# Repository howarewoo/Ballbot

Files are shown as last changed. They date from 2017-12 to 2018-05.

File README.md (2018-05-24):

 # Ballbot: a Dynamically Stable Omnidirectional Robot

A ballbot is a dynamically-stable mobile robot designed to balance on a single spherical wheel (i.e., a ball). Through its single contact point with the ground, a ballbot is omnidirectional and thus exceptionally agile, maneuverable and organic in motion compared to other ground vehicles. Its dynamic stability enables improved navigability in narrow, crowded and dynamic environments.

The ballbot works on the same principle as that of an inverted pendulum. As such, the ballbot can be broken down into three major components: The pendulum, the control system, and the drive unit. The pendulum component, and therefore the control system, can further be broken down from a single three dimensional coordinate system to pair of two dimensional coordinate systems.

Because the pendulum is broken down into two dimensional models, the control systems computes the required X and Y axis components to control the system. Using a linear quadratic regulator and discrete state space controller, the control system can use the angle from vertical to produce optimized control for the desired states. These states can be summed to represent a resultant vector in the XY plane.

This resultant vector can be converted to motor speeds though kinematic equations for the interaction between the motors, wheels, and ball.

CAPSTONE project by Adam Woo, Graham Goodwin, and Chloe Desjardins

## Mathematical Modeling

In essence, a ballbot is an omnidirectional inverted pendulum. This means that the ballbot can be broken down into two inverted pendulums that travel along the X and Y axis. The angle of the robot along these axis at any given time can be used to calculate the necessary velocity required to keep the pendulums upright.

The X and Y components can be summed to a desired resulting vector, which can be used to maintain the robots verticality in 3D space.

The state equations for an inverted pendulum can be represented as:

<p align="center">

</p>

<p align="center">

</p>

Where the variables are:

<p align="center">

</p>

These state space equations are used to produce a state space controller, where the output of the controller, , is the desired ball velocity along the X or Y axis.

These velocities can be plugged into a set of kinematic equations that calculate the required speed of each motor. The motor speeds much sum all torques around the Z axis to 0 for our system. These equations can be represented as such:

<p align="center">

</p>

<p align="center">

</p>

The scalar  accounts for the angle of the wheels relative the the center of the ball. This shifts the resultant velocity to the top surface of the ball.

To solve for the motor speeds, the inverse of the 3x3 matrix was found. When arranged to solve for the desired motor speeds, the equations look as follows:

<p align="center">

</p>

These equations can be used to calculate the desired speed of each motor in m/s, which can then be converted to steps/s based on the length of each step. The steps/s is the frequency at which pulses will be sent to the motor drivers.

Matlab was used for all of the control system modeling.

## Hardware

Here is a list of the selected hardware:

| Component | Part | Description |
| --- | --- | --- |
| Microcontroller | Teensy 3.6 | Faster processor speed, easy plug and play setup, and an extensive community make the Teensy 3.6 an ideal choice for the microcontroller over less powerful options like an Arduino Mega, or a less supported board. |
| IMU | MPU6050 | The 6 degrees of freedom supported by the MPU6050 allow for accurate angle measurements for a very cheap price. |
| Ball | 10" Stainless Steel Mirror Ball w/ Plastidip | A 10" steel ball provides a round ridged surface strong enough to support the robots chassis. The ball is coated in Plastidip, a rubberlike spray that will increase the friction on the ball. |
| Wheels | 3x 3.25" VexPro Omniwheel | Omniwheels allow for free movement perpendicular to the wheel. This allows for the development of holonomic movement systems. |
| Motors | 3x Nema 23 Stepper Motor | Stepper motors provide the high level of precision and torque at low speeds that the system will need to remain stable. |
| Motor Drivers | 3x TB6600 Stepper Motor Driver | These drivers allow the stepper motors to be controlled with only two data pins; one for direction and one for speed. |
| Battery | Gens ace 5000mAh 11.1V LiPo | The battery must be at least 9V. This battery was a highly rated battery with a large capacity, sufficient voltage, and relatively low weight. |
| Universal Battery Elimination Circuit | BW® RC Servo BEC UBEC 3A 5V | An UBEC is a voltage regulating circuit used to take power from the battery to the microprocessor. |

## Building Process

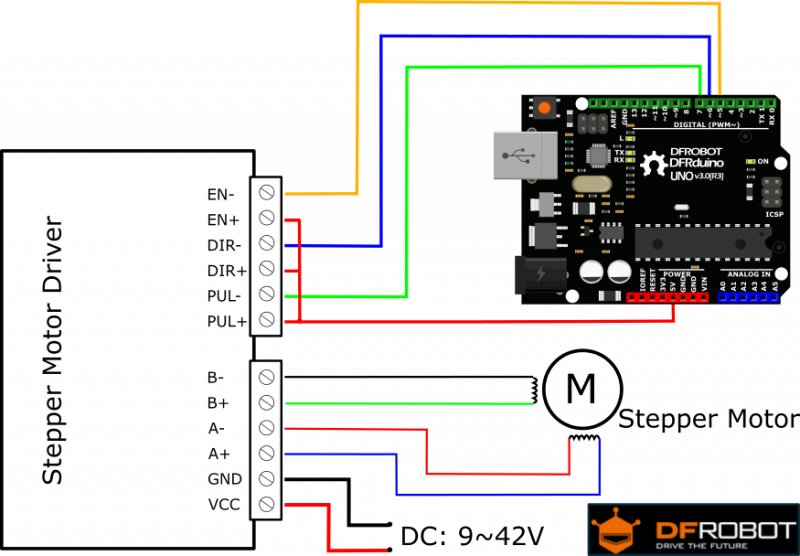
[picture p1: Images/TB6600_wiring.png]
TB6600 Wiring


The driver was manually set to the following:
- Microstepping: 1/8
- Current: 2.8A

The step pins output a square wave of varying frequencies. Pins 2, 3, and 5 where chosen because they all run on different timers. Therefore, the frequencies can be adjusted independently.

## Programming

All programming was done using the Atom text editor, Arduino IDE, and Teensyloader programs.

**Libraries**
- discreteSSC.h by Adam Woo
- quaternionFilter.h by Kris Winer
- Math.h
- Wire.h
- TimerOne.h
- FrequencyTimer2.h
- TimerThree.h

## Results

The ballbot provided limited stability for the 2D control systems. While this could be for several reasons, a likely reason for the instability is that there are forces not accounted for by a two dimensional model of the system.

The longest recorded stability of the robot was approximately 10 seconds.

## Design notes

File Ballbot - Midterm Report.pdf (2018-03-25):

### Ballbot Fall Semester Design Report:

### Design Process

Graham Goodwin, Adam Woo, Chloe Desjardins

Capstone I: ENGR 483
Professor Huang and Professor Mertens December 15th, 2017

Table of Contents

I. History of the Ballbot
In 2008, a team of graduate researchers at Carnegie Mellon University developed the first omnidirectional robot, capable of interacting in human environments. This design differed from other robotic designs in that for a robot to actively interact with human movement, an entirely different approach to locomotion must be implemented. The goal was to develop mobile robots that are safe, dynamically agile, and capable of graceful motion. The robot would be slender enough to easily maneuver in crowded, peopled environments, and readily yield when pushed around. In order to meet these design requirements, the team of researchers decided to create an intrinsically unstable robot which uses a ball for mobility. This new concept introduced the family of robotics to “ballbots.” Despite the capabilities of the omnidirectional machines known as ballbots, there has been little improvement made on the original designs.
In addition to the work done by the researchers at Carnegie Mellon University, some engineering students at ETH in Zurich have created a similar ballbot, using the concepts of stability and balance. This ballbot, named “Rezero,” has the ability to interact with humans, aims at high agility and fast movement, as well as create a hands-on experience with the Ballbot technology. Rezero’s dynamic hull allows the ballbot to display emotions such as breathing, being frightened, or waking up and going back to sleep.
As the ballbot technology continues to improve, there are a variety of ways that this type of robot can be advantageous in everyday life. For example, ball bots can serve as guides in museums or act as security monitors in public places. They can also be used as a daily aid, performing basic tasks such as transporting and delivering objects to humans. Ballbots can also be used as service robots assisting the disabled such as the blind. Due to the ballbot’s ability to navigate in cluttered environments and perform interference correction, the ballbot could potentially assist patients in hospitals.

II. Problem Definition
The primary objective of this project is to develop a single-contact, self balancing robot that is capable of omnidirectional movement.

III. Problem Evaluation
In order for this robot to perform in practical applications, several design criteria must be met. The ballbot must be slender enough to enable it to maneuver through crowded spaces. The body of the robot cannot be too wide, as the robot should take up as much walking space as a human at most. The ballbot must also be tall enough to interact with a standing human. Lastly, the ballbot needs to be capable of performing interference correction. This means that the ballbot can give in to small pushes, but then reset and continue on its trajectory. These three design goals correlate with the potential use cases for ballbots in that our ballbot will be capable of omnidirectional stabilization and agile movement in crowded environments.
We decided early on that humans should be able to easily interact with our system while standing, thus one of our primary design goals was to make the system at least three feet in height. Additionally, there would be little need for a single contact system unless it holds some advantages over multiple contact systems. A primary advantage of single contact systems is that the base can be quite narrow, even if the entire body is rather tall. This means that such systems can easily maneuver through crowded environments without sacrificing height. To play to this strength, we decided to aim for a system that would be slender, less than one foot wide.
Some goals were discussed but not established, such as speed, precision, carrying capacity, durability, interactability, and power consumption. However, we decided that these extra design goals were unnecessary or impractical for our purposes. These specifications were set as considerations, with the intention to optimize them as much as possible, but not to establish a specific requirement for project completion. With the design goals established, we moved on to address the design constraints of this project.
The first constraint established was time. The time limit for this was defined as slightly less than an academic year, accounting for presentations and analysis and the end of the year. Our group agreed that this was ample time for the projects main objective of designing a stationary balancing robot, with room to add movement or other aspects later down the line.
The second constraint addressed was cost. The Trinity College Engineering Department allocated $150 per student for their senior design projects. That means that our team of three was given a $450 budget. A quick look at the required equipment we might need to buy allowed us to estimate that we would have more than enough money to complete this project.

IV. Alternatives
Before weighing alternative parts for our system, we first had to decide on an overall design of the system. We looked at several examples of existing ballbots, some of which are displayed below:

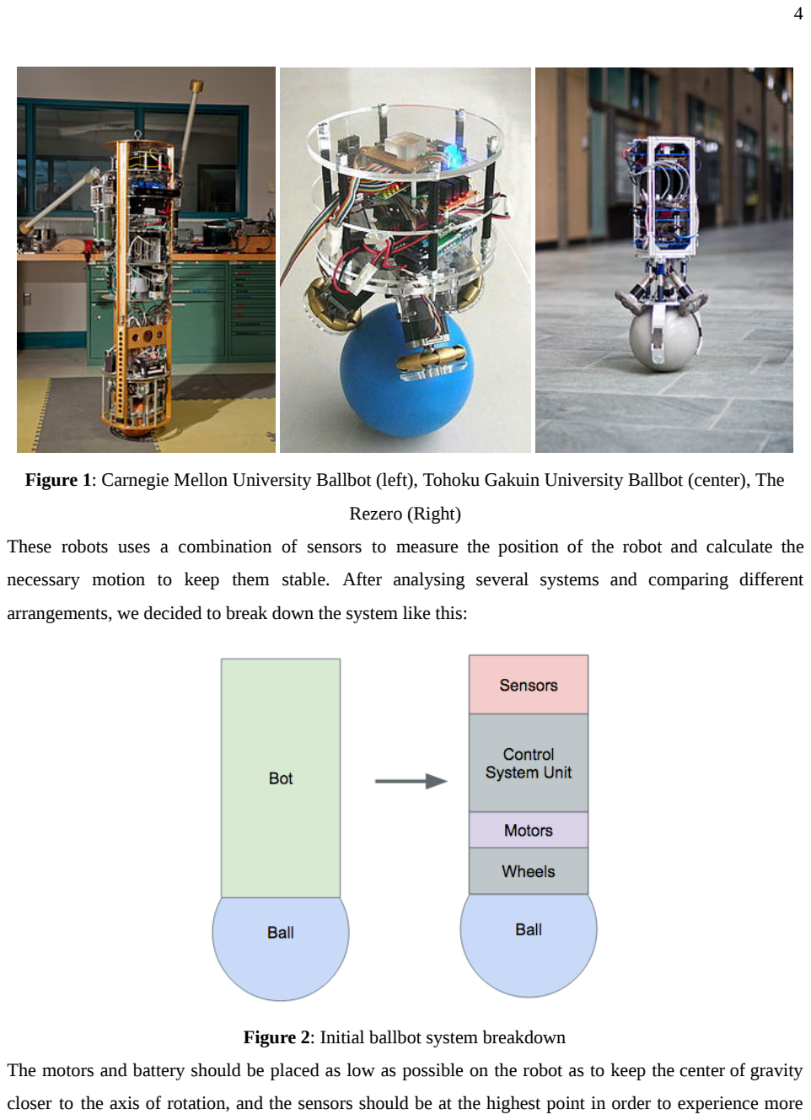
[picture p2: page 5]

Figure 1: Carnegie Mellon University Ballbot (left), Tohoku Gakuin University Ballbot (center), The Rezero (Right)
These robots uses a combination of sensors to measure the position of the robot and calculate the necessary motion to keep them stable. After analysing several systems and comparing different arrangements, we decided to break down the system like this:

Figure 2: Initial ballbot system breakdown The motors and battery should be placed as low as possible on the robot as to keep the center of gravity closer to the axis of rotation, and the sensors should be at the highest point in order to experience more exaggerated movement for measurement. The components of the control system should weigh little enough that their placement should have a negligible impact on the system’s stability.
With a tentative structure of the robot designed, we began analysing alternatives for each component.

The Ball
From our design goals, we knew we wanted the base of the system to be less than one food wide, and thus we only considered types of balls whose diameters were about that wide.
From our problem evaluation, we knew that a lightweight ball would require less torque from the motors to move. Thus, we tried to strike a balance between weight and functionality when choosing the ball. We researched the following alternatives, and listed the pros and cons of each:
Table 1: Ball Alternatives with Pros and Cons
Name | Pros | Cons
Bowling Ball | -rigid surface -good quality control (close to perfectly spherical) | -slippery surface -requires excessive torque from motors -expensive (~$40)
Steel “Mirror Ball” Lawn Ornament | -hollow (less torque required) -rigid surface | -slippery surface -expensive (~$30)
Hollow Plastic Ball | -low mass (little torque required for motion) -Inexpensive (<$10) | -flexible surface -slippery surface
Basketball | Inexpensive (~$10) -low mass -surface has high coefficient of friction | -ridges on surface introduce error/potential failure of system -not entirely spherical

While each of the alternatives above have their own merits, we decided that we could best work around the shortcomings of the steel mirror ball. The bowling ball had all of the shortcomings of the mirror ball in addition to the excessive torque requirements it would place on the motors. The benefits did not seem to outweigh this issue, so we eliminated the bowling ball alternative. A bowling ball is also relatively expensive ($40), thus we decided that this was not the best fit for our system.
The only real benefit of the hollow plastic ball was that it was extremely cheap, however, since the other alternatives were well within our budget, price was not a major concern. So we quickly eliminated the plastic ball alternative as well.
The basketball was a close contender with the mirror ball. It would provide good grip for the wheels on the surface of the ball, and was lighter than the mirror ball by about 0.3 kg. However, the ridges on the basketball would introduce error into our system. It would be near impossible to predict when the wheels would be rolling over one of the basketball ridges, and thus some varying degree of unknown error would be introduced. We were already getting a sense of the complexity of the mathematical system behind the ballbot, so we decided to pursue the mirror ball alternative. To counteract the slippery surface of the mirror ball, we came up with the idea of coating it in plastic spray. This would eliminate the surface grip problem, and since the price was within our original cost estimate, we were satisfied with this alternative.
Chosen Alternative: Steel mirror ball with plasti-dip coated surface
- Size: 10” diameter (near perfect sphere)
- Weight: 0.91 kg
- Total Cost: $45 ($35 + $10 for plasti-dip)

The Microcontroller
In order to control a dynamically stable system, the microprocessor needs to be able to communicate with sensors, calculate the raw data through a control system, and send the control signals to the motors extremely quickly. The main issue with this design is that the control system is complex, involving several trigonometric calculations and filters which are very processor intensive. The microcontroller needs to have a processor capable of computing these calculations quickly.
Additionally, we wanted to program the controller using our language of choice, C++. We use the Atom text editor plugin PlatformIO to write, build, and upload our programs to various microcontrollers. While this is not a restriction for our system, it was an ease of use factor which influenced our decision. To decide on a microcontroller, we researched what had been used for several other ballbots. The main alternatives to decide between were as follows:

Table 2: Microcontroller Alternatives with Pros and Cons

Name | Pros | Cons
Arduino Mega | ● already owned (~$10 otherwise) ● PlatformIO bootloader compatible ● 54 programmable pins | ● 8 Mhz clock speed
Raspberry Pi 3 Model B | ● 1.2 GHz clock speed ● 26 programmable pins ● Large community ● USB power ● Expandable | ● expensive (~$35) ● Complex library setup ● Not PlatformIO compatible
Teensy 3.6 | ● 180 MHz clock speed ● PlatformIO bootloader compatible ● 32 programmable pins ● Arduino library compatible ● Micro USB power port | ● expensive (~$40)

After extensive research on what microcontroller would be the most efficient to use, we decided to choose the Teensy 3.6. Initially, we were going to use a Raspberry Pi because of its familiarity and its extensive community support. However, after performing further problem evaluation, we decided to go with the Teensy 3.6 due to its larger number of programmable pins (32), high processing speed (180 MHz), and good compatibility with our IMU and it’s fusion libraries (more on this later).
Chosen Alternative: Teensy 3.6
- Processor Speed: 180 MHz
- Cost: $40

The Ball Drive System
The parts in contact with the ball needs to allow movement in all directions. The parts cannot restrict range of motion in any why. The type of ball drive system was relatively easy to chose, as majority of the alternatives were either too difficult to build, or would not work all together.
Table 3: Wheel Alternatives with Pros and Cons
Name | Pros | Cons
Partially Sliding Rollers | ● Inexpensive | ● Cannot be purchased ● Difficult to build
Omni-wheels | ● Easily purchased ● Passive lateral movement | ● Low strength ratings for cheaper models ● Non standard mounting options
Mecanum wheels | ● Easily purchased ● Inexpensive ● Higher strength ratings | ● No passive lateral movement (active movement only)
Spherical Induction Motor | ● Single moving part ● Highly accurate motion | ● Cannot be bought ● Very complex to build

Omni wheels were the only movement system that was feasible for this project. The mecanum wheels restricted movement laterally, and the other two systems were two difficult to design in the given time period. While the type of ball drive system itself was easy to chose, the design of this system was more difficult to agree upon. We looked at several different orientations for the wheels:

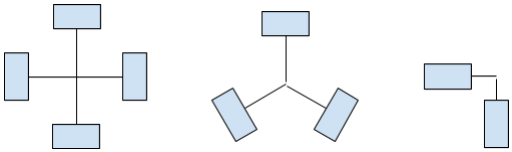
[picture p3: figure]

Figure 3:Various wheel arrangements

The first orientation we looked at was the four wheeled design which maps two wheels to each axis. This was a good design and easy to control. However, omni wheels and the motors required to drive them are expensive, as well as heavy. To cut down on these costs, we looked at a two wheeled model which used point the wheels towards the center of the robot. This gave us control over the x and y axis, but removed the possibility of rotation. The compromise was a three wheeled design spaced evenly apart, which the wheels placed perpendicularly to the robot’s center. The wheels would be angled at 45 degrees and placed 45 degrees from the ball’s center to maximize control over all axis of rotation.

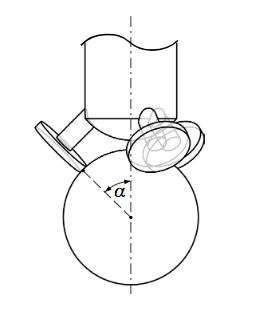
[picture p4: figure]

Figure 4: The three wheeled design of the ball drive system, where α=45° This design maximizes control over the ball, while minimizing the weight and cost of the system. Chosen Alternative: Three omni wheels
- Manufacturer: Vex Pro
- Size: 3.25” diameter
- Total Weight: 0.54 kg (3 wheels, 0.18 kg each)
- Total Cost: $54 (3 wheels @ $18 each)

The Angle Measurements Devices
For these type of projects, inertial measurement units (IMUs) are the most widely used by far. There really were no other alternatives to decide between for measuring the robot angle from vertical. Among IMUs, the MPU6050 and MPU9250 were the two alternatives we considered.

Table 4: IMU Alternatives with Pros and Cons

Name | Pros | Cons
MPU6050 | ● 6 axis (accelerometer, gyroscope) ● Inexpensive ($7) | ● -no magnetometer (cannot measure compass direction)
MPU9250 | ● 9 axis (accelerometer, gyroscope, magnetometer) ● More precise measurement after filter | ● More complex filters ● Less community support ● Less board compatibility ● Slightly more expensive ($10)

The MPU9250 was the most suitable option compared to the MPU6050. Although the MPU6050 is three dollars cheaper than the MPU9250, the MPU9520 has 9 axes with an accelerometer, gyroscope and magnetometer. The MPU9520 is also capable of measuring compass direction. When considering our future goals for the movement of our ballbot, these additional capabilities of the MPU9520 were enticing and seemed more practical for our ballbot design. The price of the MPU9520 was also still within our economic means.
Chosen Alternative: MPU9250
- Functionality: 3-axis accelerometer (angular acceleration), 3-axis gyroscope (angular velocity), 3-axis magnetometer (compass direction)
- Cost: $10

The Motors
To drive the wheels, we required motors with relatively high torque at low speeds that could handle precise movement and change direction quickly. This indicated to us that stepper motors would likely be the best choice, though we did consider brushless DC motors as well.

Table 5: Motor Alternatives with Pros and Cons

Name | Pros | Cons
DC Brushless Motors | ● Inexpensive ● High RPM ● PWM | ● Lower torque ● Ramping acceleration
Stepper Motors | ● High torque at low speeds ● Precision movements | ● More expensive ● No PWM

We decided to use stepper motors for our system, because of their high torque at low speeds and precise movement options. We decided to use an a4988 stepper motor driver to control and power them. We also decided to use a motor that fits the NEMA 23 standard. This allows us to start designing the mounting hardware, even though we do not know the exact model we will be using.
We have not yet decided on a model because we want to make sure the rated torque is high enough for our system, which requires the math modeling to be completed first. The NEMA 23 comes in a variety of lengths, the longer the motor the higher the torque. We will purchase the motors early next semester.

### Ballbot Fall Semester Design Report:

### Full System Design Description

Graham Goodwin, Adam Woo, Chloe Desjardins

ENGR 483: Engineering Capstone I

December 15, 2017

Introduction
The following document details our current full-system design. It serves as an overview of the subsystems we have identified, as well as the completion levels of those systems.

Current System Design
We identified the following subsystems of the ballbot:
1. Chassis
2. Inertial Measurement Unit System (9-axis IMU)
3. State observer system (microprocessor)
4. Controller system (microprocessor)
5. Ball drive system
6. Power system
After going through the problem evaluation process and weighing alternatives, we arrived at our current full-system design. A physical layout of the system can be seen below.

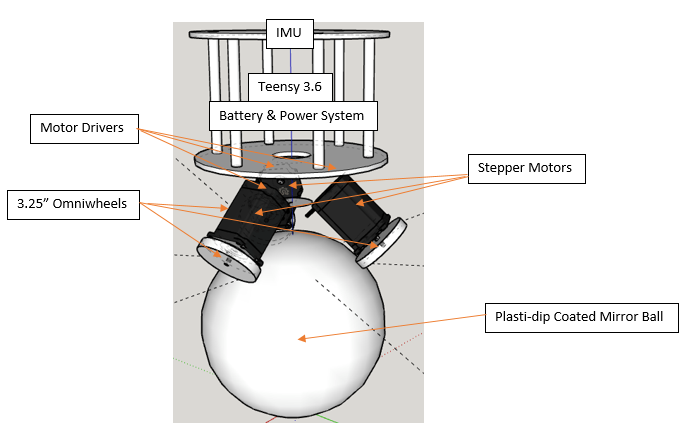
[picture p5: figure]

Figure 5: Full-system Physical Layout

We also constructed a block diagram depicting how the system components will interact (seen below).

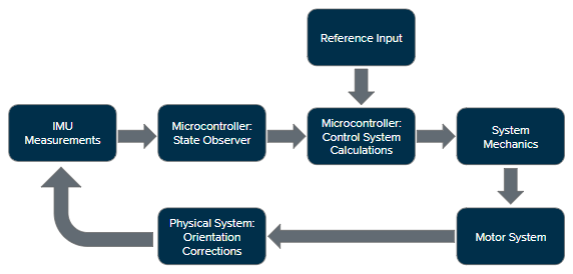
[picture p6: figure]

Figure 6: Full system block diagram

Chassis
The chassis design for the system was kept very simple with only the purpose of housing the other components. We chose a 10” diameter circular platform design that can be easily raised and lowered depending on the size of the parts. One platform will attach to the motor mounts, and hold the battery and motor drivers on it. The middle platform will hold the microprocessor, and the top platform will have the IMU mounted to the bottom of it. The platforms will be held together using six ¼” threaded rod and held in place with twelve ¼” nuts and washers for each platform. This allows the platforms to be moved according to the needs of the system, but still remain secure when desired.

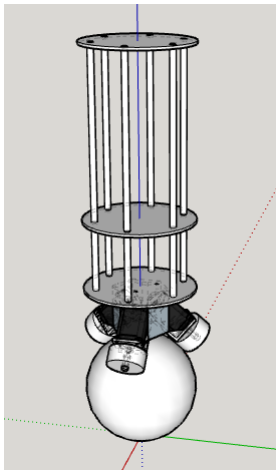
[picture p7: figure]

Figure 7: Full size CAD model of the ballbot

IMU System
The MPU9250 consists of an accelerometer, gyroscope, and magnetometer, which read angular acceleration, velocity, and compass readings respectively and communicates them to the microcontroller using I2C. These sensors supply three raw data points each, one for each axis, for a total of nine data points. In order to convert these data points into understandable Euler angles (pitch, roll, and yaw), we need to first put these points through sensor fusion, a method of combining the readings to reduce noise and minimize calculation error. Our chosen method of sensor fusion was Sebastian Madgwick’s Orientation Filter, seen below:

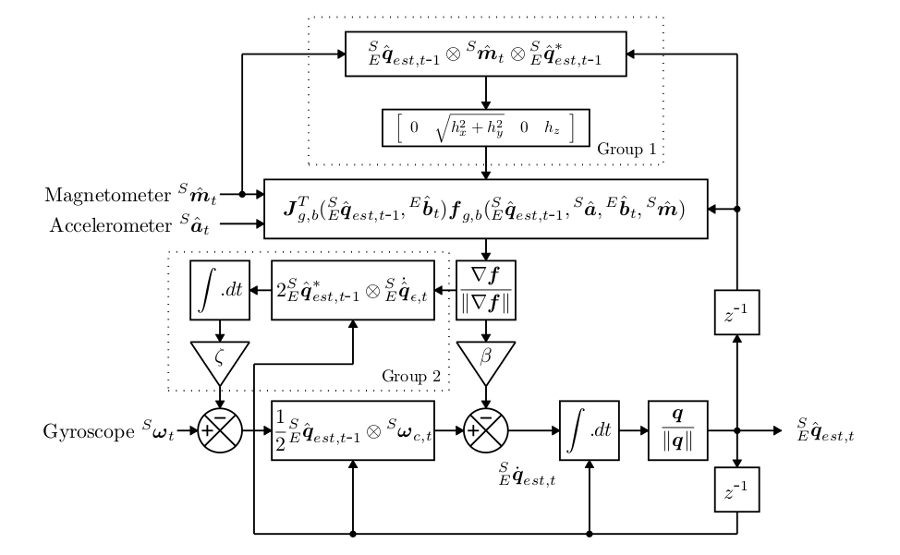
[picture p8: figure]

Figure 8: Sebastian Madgwick’s Orientation Filter This sensor fusion algorithm inputs the data from the three measurement tools and outputs a quaternion, which is essentially a four dimensional unit vector. This quaternion can be used to find Pitch, Roll, and Yaw using the following equations:

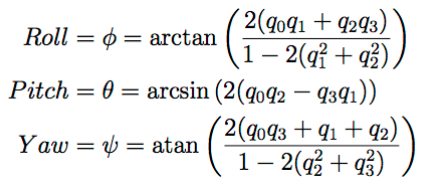
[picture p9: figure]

This method was chosen because it is one of the most accurate methods for calculating the angular position. It is also open source which allowed us to use pre existing C++ libraries and modify them for our specific IMU. We have already implemented this our our microprocessor and tested the accuracy of our readings. Sebastian Madgwick claims that this algorithm is precise to less than a degree of error.

State Observer
The state observer system is a project for next semester, but we know that it will take in the Euler angles generated by the IMU calculations and output the system states, i.e. the angle from vertical and its velocity, and the angular position of the ball and it’s velocity.

Control System
We have explored several options for controlling our system, but have yet to decide on a final method. The first method would be to use a proportional integral derivative control (PID) to control by calculating the required gains for our unique transfer function, and then refining the controls empirically. We also explored linear quadratic regulator (LQR) controls, which is an optimizing form of control that aims to minimize some user-defined cost function. In our case, that cost function would be the systems angle from vertical.
Regardless of the control method, the inputs would be the desired angles from vertical in the z-x and z-y planes. The feedback would come from the IMU which depending on the difference between the desired angle and the actual angles, return the required x and y velocities for the ball to stabilize the system. The ball drive system will take the desired x and y velocities and convert them to the appropriate motor speeds to move the ball the desired resultant vector.

Ball Drive System
The ball drive system is made up of the motor drivers, the motors, and the wheels. The a4988 stepper motor drivers power the motors and control their speed via their connection to the microprocessor. Stepper motors have a high torque at low speeds which will allow for quick changes of direction. The wheels are connected the motors by a custom designed 3d printed wheel hub.
We opted for a three wheeled design to cut down on weight and cost, as opposed to a four wheeled design. Despite the mechanical advantages of this orientation this design does presents a difficulty in controlling the motors there are no two wheels mapped to each axis. This means that a series of motor speed equations will need to be developed to move the ball correctly. By drawing out the wheel orientations as such:

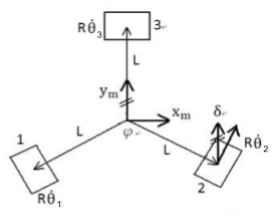
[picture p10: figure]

Figure 9. Kinematics of robot movement in the x-y plane

Here, δ is the angle between the wheel and the axle (90°), and φ is the angle between the center of each wheel (120°). This leaves us with these equations:
θ̇1 = R

ẋ− ẏ+Lϕ̇ 2

1
| 2

√3

θ̇2 = R

ẋ+ ẏ+Lϕ̇ 2

1
| 2

√3

θ̇3 = R

ẋ+Lϕ̇

Where θ̇ is the angular velocity of the motor, L is the distance from the center of the robot, and R is the

wheel radius. We can find trigonometric equations that sum the velocity vectors of the motors to give a single velocity vector in a desired direction from the robot’s center:

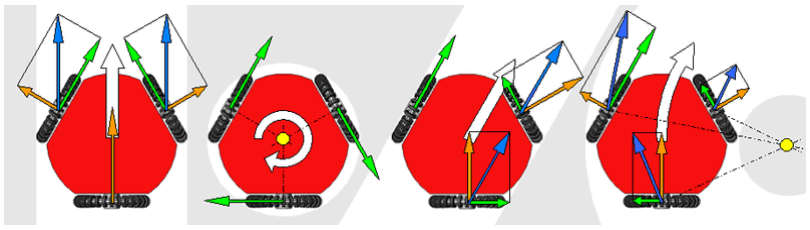
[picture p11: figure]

http://3.bp.blogspot.com/_a_6DwTj3ij0/TRxY3TovHHI/AAAAAAAAAGc/OVVlBWgrc5g/s1600/800px-robot_omnidirectional_movement_spe edvectors.gif
Figure 10: Examples of potential movement patterns for the ball bot as a sum of the wheel velocities (green arrows)

Because we know the size of our wheels and our ball, we can find the values of L and R to plug into these equations:
L = √ | .755in

π

√10in −(5in(sin(45)))
2 | 2 ≈ 1
R = | .625in
2

3.25in = 1

Which leaves us with:
θ̇1 = | .308ẋ | .533ẏ | .08ϕ 1.625

ẋ− ẏ+1.755ϕ̇ 2

1
2

√3
≈ 0 | − 0 | + 1
θ̇2 = | 1.625

ẋ+ ẏ+1.755ϕ̇ 2

1
2

√3

## ≈ 0.308ẋ+ 0.533ẏ+ 1.08ϕ

θ̇3 = 1.625

.08ϕ

ẋ+1.755ϕ̇
≈

ẋ
1.625 + 1

These equations can be used to take the desired system velocities given by the controller, and convert them into equivalent motor speeds.
The omni wheels have a rubber texture on the rollers, and the ball is coated in plastidip to increase its traction.

Power System
The power system, so far has been an afterthought. We know that the motors operate on 5.4V at 1.5A, while the Teensy 3.6 runs on a 5V input. We need to do more research on the battery and power supply system, but the basic wiring for the motors and drivers will look like this:

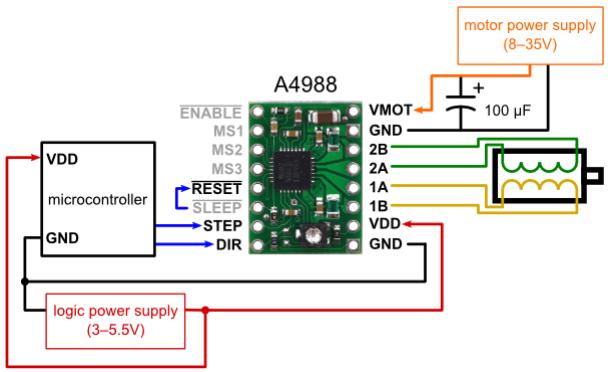
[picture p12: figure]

Figure 11: Circuit diagram for the a4988 motor drivers

Math Modeling
We started with a 2D planar model of the system. We start with a 2D model because the xz and yz planes of the robot are identical. The full system is then controlled by breaking each motor force into components in the xz and yz planes.

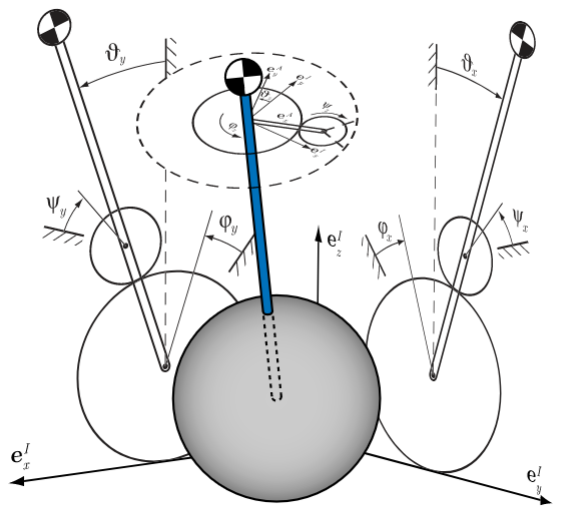
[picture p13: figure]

Figure 12: The 2D breakdown of the 3D system Analyzing the system in this manner will give us a desired velocity for the x and y components and sent direction to the motor equations. The predicted result will be 3D stabilization as the combination its components.
We have not yet explored the intricacies of coupling these planar models, but the hope is that this method will give a close enough estimation of the system controls to be modified empirically.

System Completion Percents
To assess our work over the past semester, as well as clarify what needs to be done going forward, we assigned completion levels to each of the subsystems we identified. For each subsystem, a percentage has been assigned to signify how complete it is, and a second percentage has been assigned to show if the physical components have been acquired yet. These can be seen below in Table 1, along with some details on what is complete, and what is left to do.

Table 6: Subsystem Physical and Design Completion Levels

Name of System | Level of Completion | Parts Acquired | Details
Chassis | 80% | 0% | CAD model finished, parts are not 3D printed
IMU System | 100% | 100% | IMU purchased, code implemented to output pitch, roll, yaw
State Observer | 10% | N/A (microprocessor) | States decided upon, need to research how to build state observer
Controller System | 50% | N/A (microprocessor) | PID and LQR researched, need to incorporate it into our model
Ball Drive System | 80% | 60% | Ball, plasti-dip, omniwheels and motor drivers purchased, need to purchase motors
Power System | 10% | 0% | Need to decide on and purchase battery
Math Modeling | 60% | N/A | 2D model completed, need to research coupling between 2D planar models

Spring Semester Goals
After assessing our progress thus far, we have a variety of goals that must be considered and achieved for the spring semester. Firstly, we need to complete the modeling of the system such as the Computer Assisted Design (CAD) modeling and the design of the chassis. After performing various calculations on the motors this semester, we have three separate motor equations, one for each motor. These motors that will be used to move the omni-wheels must still be purchased. Although we have already acquired majority of the hardware for our system, we still need to obtain several components such as the battery. Once all necessary parts are secured, we can then assemble the physical system. We will also complete the controller design and implement the control in code using C/C++. Once all of these goals are achieved, we will then proceed to test the system and tune the controller in order to achieve stability. Lastly, if time permits, we will ultimately implement remote controls or tracking for our ballbot.

Appendix
Meeting Minutes
Below is a summary of our meeting minutes with Professor Huang. We met (officially) every Friday at 10 am in order to discuss our progress and set our goals for the following week.

Capstone Meeting: Friday 11/03/17 - all members present
Plaster dip or rubber spray for the ball - cheapest
Stepper motors - need enough torque to get ball moving
Need stepper motor controllers
Need inputs
Stepper motor driver - power driver individually, need 4 pins, can do it directly from power source Need some sort of wedge to provide for angles, mount it to bottom of platform - use aluminum

Ball - $35
-10 in diameter

Omni-wheels -
-2-4 in in diameter?

How are we going to mount omni-wheels to the motors?
-Axle mount?

Arduino coded in C++ so we can convert to Raspberry Pi if needed -Arduino is cheaper than Raspberry Pi
-Make sure it works with Arduino first because we are all familiar with it

Want a prototype by the end of the semester!!!

Batteries
RC batteries

Acrylic components, 3D printing a prototype test base

Equations
Kinematic equations for motors, not sure if we need them to actually make the robot work, throw PID onto board and it will compensate
-Need to model how our control inputs are going to affect our states
Model using physical equations- how the motors will affect the ball moving around, torques and pendulums
Control theory- look into building an observer, get into algebra and talk about observability and controllability space

Look over theses for designing a ball bot to get an idea of what equations of motions will look like

Things we need to accomplish for next week:
-Look into ACS stuff
-Modeling/Kinematic Equations
-Design chassis (base)
-Axle mounts
-Ordering parts: ball, new IMUs, motors, driver chip A4888 -Find suitable batteries

Assignments:
Graham
-Modeling/Kinematic Equations

Adam
-Design chassis (axle mount)
-Begin coding
-Kinematics Equations for motor speed

Chloe
-Look into ACS stuff
-Find suitable batteries

Mutual:
Ordering ball, IMUs, motors, driver A4888, rubber coat
-Order ball, IMUs, driver A4888, rubber coat ($5) hold off on omni-wheels

Meeting minutes Friday 11/10/17 - all members present

- Model 3 motors on the ball separately using trigonometry in 3D then sum them together -Forces from the wheels
-Pendulum falling in the plane
-Then put these equations in block diagram as parameters
-3 planar model method
- Write state space equations, block diagram, feedback of 1 -Design for particular step response
-8 states total
- Response time - assume instantaneous
- Estimator? LQR/LQG?
- PID Controller

For the next 2 weeks:
-Motors
-Wheels
-Consider use cases
-Continue math modeling, research coding techniques

Graham:
-Continue math modeling

Adam:
-Researching coding techniques
-CAD model chassis
-CAD model and print custom mounting hardware

Chloe:
-Look into use cases
-Batteries

Mutual:
Purchase motors and omni-wheels

Meeting Minutes Friday November 17 - all members present
- Raspberry pi came, MPU
- More math modeling - turn into 3D
- Inverted pendulum project?
- NiMH 3-5 Ah - look up what hobbyists have used
- Lithium iron phosphate - any 5 Ah
- Buy batteries cheap to buy a few and keep cycling them
- Mechanical model by the end of the semester in google sketch-up
- Bought: raspberry pi, plasti-dip, ball, smaller electronics
- Stepper motors, have drivers
- Omni-wheels and motors are most important
- Heavier or lighter wheel based on inertia?
- Omni-wheels on the smaller side to get a faster response, need faster RPM : 2-4 in in diameter

Progress presentation for next Tuesday (post Thanksgiving) - start working on this
Continue with what we are doing….

Things we need to do:
-Buy omni-wheels, motors, batteries
-hobbyking.com, look at best selling battery and buy it -CAD modeling, MPU testing
-Start using Raspberry pi

Meeting Minutes 12/4/17 - Professor Mertens, all members present
- Need to calculate max angular acceleration that we want to impart on the ball
- Find torque in relation to axis of the ball
- The torque that the motor needs depends on the motor arm
- Ball moves by applying a tangential force
- Ɑ = ??, how quickly must we accelerate the ball?
- **Need to account for slippage**
- Quantify our design criteria - create a robust theoretical model
- “Subprojects” - a) dynamic analysis of the moving ball, b) microprocessor, c) motors, d) feedback loop
- For Traveler’s Presentation on 12/12/17: Show current design, components, here is what we have completed…
- Make sure to highlight which topic from the outline we are discussing during the presentation...Makes it easier for the listener to follow along and makes things less complicated

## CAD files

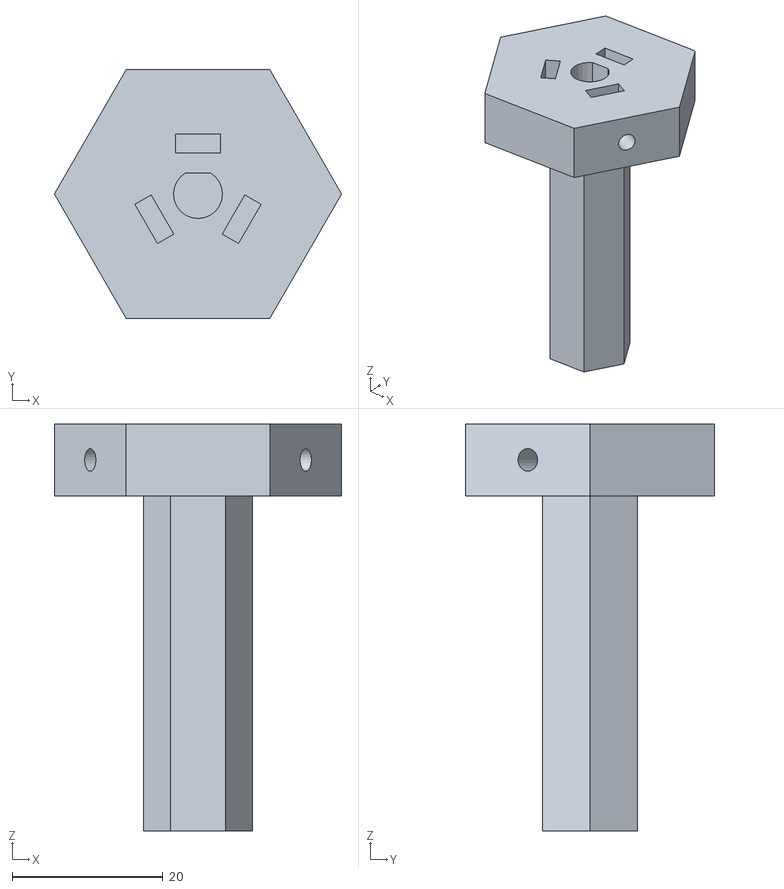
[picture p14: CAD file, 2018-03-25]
CAD/Wheel Mount.stl
38.1 x 33.0 x 54.0

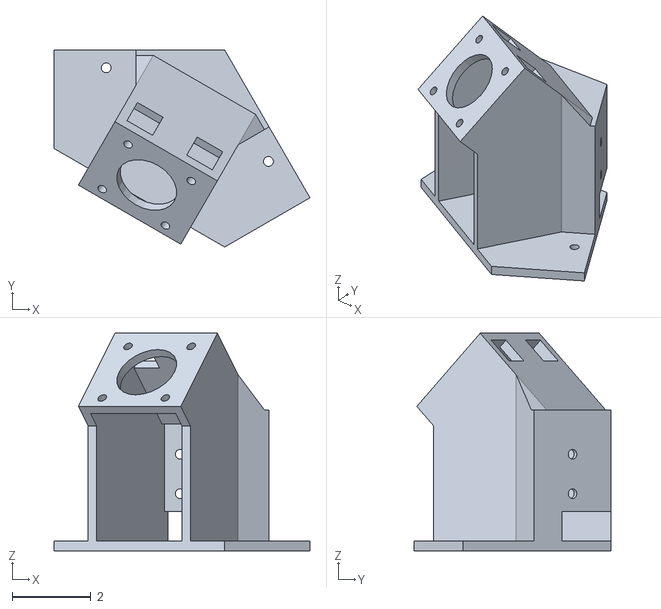
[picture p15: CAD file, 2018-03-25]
CAD/Ballbot Motor Mount v.3.stl
6.50 x 5.00 x 5.52

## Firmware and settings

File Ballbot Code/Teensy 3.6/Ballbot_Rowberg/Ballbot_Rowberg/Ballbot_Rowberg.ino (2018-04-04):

/* Ballbot_MPU6050.ino
*
* Omnidirectional Ballbot control system with 3-axis PID controls using the
* MPU6050 IMU
*
* Written by Adam Woo
*
* MIT License
*/

#include "math.h"
#include "PID_v1.h"
#include "FrequencyTimer2.h"
#include "TimerOne.h"
#include "TimerThree.h"

#define ROBOT_HEIGHT 31 //inches
#define WHEEL_RADIUS 1.625
#define STEPS_PER_ROTATION 6400 //steps
#define MAX_SPEED 120 //inches per second
#define MAX_FREQ 2000 //component steps per second
#define ACCEL 2000 //steps per second


int sampleRate =  10000; //microseconds
bool printFlag = false;

#define DIR1 12
#define STEP1 2
#define DIR2 24
#define STEP2 3
#define DIR3 26
#define STEP3 5

//Three PID controllers; one for each axis of rotation
//Define Variables we'll be connecting to
double CurrentAngleX, OutputSpeedX, DesiredAngleX = 0;
double CurrentAngleY, OutputSpeedY, DesiredAngleY = 0;
double CurrentAngleZ, OutputSpeedZ, DesiredAngleZ = 0;
double Kp_x=10, Kp_y=10, Kp_z=10;
double Ki_x=1, Ki_y=1, Ki_z=1;
double Kd_x=2, Kd_y=2, Kd_z=2;

//Specify the links and initial tuning parameters
PID xPID(&CurrentAngleX, &OutputSpeedX, &DesiredAngleX, Kp_x, Ki_x, Kd_x, DIRECT);
PID yPID(&CurrentAngleY, &OutputSpeedY, &DesiredAngleY, Kp_y, Ki_y, Kd_y, DIRECT);
PID zPID(&CurrentAngleZ, &OutputSpeedZ, &DesiredAngleZ, Kp_z, Ki_z, Kd_z, DIRECT);

#define AHRS true         // Set to false for basic data read
#define SerialDebug true  // Set to true to get Serial output for debugging

// -----------------------------------------------------------------------------
// Need this to compile for some reason... No idea why. Think it has something
// to do with the way the Teensy loader works
extern "C"{
  int _getpid(){ return -1;}
  int _kill(int pid, int sig){ return -1; }
  int _write(){return -1;}
}
// -----------------------------------------------------------------------------

// Pin definitions
int Pin = 12;  // These can be changed, 2 and 3 are the Arduinos ext int pins
int RPM = 0;

double speed1, speed2, speed3;
double timer = 0, timerstart, timerend;
double yaw, pitch, roll;
int currentSpeed1, currentSpeed2, currentSpeed3;

// I2C device class (I2Cdev) demonstration Arduino sketch for MPU6050 class using DMP (MotionApps v2.0)
// 6/21/2012 by Jeff Rowberg <jeff@rowberg.net>
// Updates should (hopefully) always be available at https://github.com/jrowberg/i2cdevlib
//
// Changelog:
//      2013-05-08 - added seamless Fastwire support
//                 - added note about gyro calibration
//      2012-06-21 - added note about Arduino 1.0.1 + Leonardo compatibility error
//      2012-06-20 - improved FIFO overflow handling and simplified read process
//      2012-06-19 - completely rearranged DMP initialization code and simplification
//      2012-06-13 - pull gyro and accel data from FIFO packet instead of reading directly
//      2012-06-09 - fix broken FIFO read sequence and change interrupt detection to RISING
//      2012-06-05 - add gravity-compensated initial reference frame acceleration output
//                 - add 3D math helper file to DMP6 example sketch
//                 - add Euler output and Yaw/Pitch/Roll output formats
//      2012-06-04 - remove accel offset clearing for better results (thanks Sungon Lee)
//      2012-06-01 - fixed gyro sensitivity to be 2000 deg/sec instead of 250
//      2012-05-30 - basic DMP initialization working

/* ============================================
I2Cdev device library code is placed under the MIT license
Copyright (c) 2012 Jeff Rowberg

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
THE SOFTWARE IS PROVIDED "AS IS", WITHOUT WARRANTY OF ANY KIND, EXPRESS OR
IMPLIED, INCLUDING BUT NOT LIMITED TO THE WARRANTIES OF MERCHANTABILITY,
FITNESS FOR A PARTICULAR PURPOSE AND NONINFRINGEMENT. IN NO EVENT SHALL THE
AUTHORS OR COPYRIGHT HOLDERS BE LIABLE FOR ANY CLAIM, DAMAGES OR OTHER
LIABILITY, WHETHER IN AN ACTION OF CONTRACT, TORT OR OTHERWISE, ARISING FROM,
OUT OF OR IN CONNECTION WITH THE SOFTWARE OR THE USE OR OTHER DEALINGS IN
THE SOFTWARE.
===============================================
*/

// I2Cdev and MPU6050 must be installed as libraries, or else the .cpp/.h files
// for both classes must be in the include path of your project
#include "I2Cdev.h"

#include "MPU6050_6Axis_MotionApps20.h"
//#include "MPU6050.h" // not necessary if using MotionApps include file

// Arduino Wire library is required if I2Cdev I2CDEV_ARDUINO_WIRE implementation
// is used in I2Cdev.h
#if I2CDEV_IMPLEMENTATION == I2CDEV_ARDUINO_WIRE
    #include "Wire.h"
#endif

// class default I2C address is 0x68
// specific I2C addresses may be passed as a parameter here
// AD0 low = 0x68 (default for SparkFun breakout and InvenSense evaluation board)
// AD0 high = 0x69
MPU6050 mpu;
//MPU6050 mpu(0x69); // <-- use for AD0 high

/* =========================================================================
   NOTE: In addition to connection 3.3v, GND, SDA, and SCL, this sketch
   depends on the MPU-6050's INT pin being connected to the Arduino's
   external interrupt #0 pin. On the Arduino Uno and Mega 2560, this is
   digital I/O pin 2.
 * ========================================================================= */

/* =========================================================================
   NOTE: Arduino v1.0.1 with the Leonardo board generates a compile error
   when using Serial.write(buf, len). The Teapot output uses this method.
   The solution requires a modification to the Arduino USBAPI.h file, which
   is fortunately simple, but annoying. This will be fixed in the next IDE
   release. For more info, see these links:

   http://arduino.cc/forum/index.php/topic,109987.0.html
   http://code.google.com/p/arduino/issues/detail?id=958
 * ========================================================================= */



// uncomment "OUTPUT_READABLE_QUATERNION" if you want to see the actual
// quaternion components in a [w, x, y, z] format (not best for parsing
// on a remote host such as Processing or something though)
//#define OUTPUT_READABLE_QUATERNION

// uncomment "OUTPUT_READABLE_EULER" if you want to see Euler angles
// (in degrees) calculated from the quaternions coming from the FIFO.
// Note that Euler angles suffer from gimbal lock (for more info, see
// http://en.wikipedia.org/wiki/Gimbal_lock)
//#define OUTPUT_READABLE_EULER

// uncomment "OUTPUT_READABLE_YAWPITCHROLL" if you want to see the yaw/
// pitch/roll angles (in degrees) calculated from the quaternions coming
// from the FIFO. Note this also requires gravity vector calculations.
// Also note that yaw/pitch/roll angles suffer from gimbal lock (for
// more info, see: http://en.wikipedia.org/wiki/Gimbal_lock)
#define OUTPUT_READABLE_YAWPITCHROLL

// uncomment "OUTPUT_READABLE_REALACCEL" if you want to see acceleration
// components with gravity removed. This acceleration reference frame is
// not compensated for orientation, so +X is always +X according to the
// sensor, just without the effects of gravity. If you want acceleration
// compensated for orientation, us OUTPUT_READABLE_WORLDACCEL instead.
//#define OUTPUT_READABLE_REALACCEL

// uncomment "OUTPUT_READABLE_WORLDACCEL" if you want to see acceleration
// components with gravity removed and adjusted for the world frame of
// reference (yaw is relative to initial orientation, since no magnetometer
// is present in this case). Could be quite handy in some cases.
//#define OUTPUT_READABLE_WORLDACCEL

// uncomment "OUTPUT_TEAPOT" if you want output that matches the
// format used for the InvenSense teapot demo
//#define OUTPUT_TEAPOT



#define INTERRUPT_PIN 0  // use pin 2 on Arduino Uno & most boards
#define LED_PIN 13 // (Arduino is 13, Teensy is 11, Teensy++ is 6)
bool blinkState = false;

// MPU control/status vars
bool dmpReady = false;  // set true if DMP init was successful
uint8_t mpuIntStatus;   // holds actual interrupt status byte from MPU
uint8_t devStatus;      // return status after each device operation (0 = success, !0 = error)
uint16_t packetSize;    // expected DMP packet size (default is 42 bytes)
uint16_t fifoCount;     // count of all bytes currently in FIFO
uint8_t fifoBuffer[64]; // FIFO storage buffer

// orientation/motion vars
Quaternion q;           // [w, x, y, z]         quaternion container
VectorInt16 aa;         // [x, y, z]            accel sensor measurements
VectorInt16 aaReal;     // [x, y, z]            gravity-free accel sensor measurements
VectorInt16 aaWorld;    // [x, y, z]            world-frame accel sensor measurements
VectorFloat gravity;    // [x, y, z]            gravity vector
float euler[3];         // [psi, theta, phi]    Euler angle container
float ypr[3];           // [yaw, pitch, roll]   yaw/pitch/roll container and gravity vector

// packet structure for InvenSense teapot demo
uint8_t teapotPacket[14] = { '$', 0x02, 0,0, 0,0, 0,0, 0,0, 0x00, 0x00, '\r', '\n' };



// ================================================================
// ===               INTERRUPT DETECTION ROUTINE                ===
// ================================================================

volatile bool mpuInterrupt = false;     // indicates whether MPU interrupt pin has gone high
void dmpDataReady() {
    mpuInterrupt = true;
}



// ================================================================
// ===                      INITIAL SETUP                       ===
// ================================================================

void setupIMU() {
    // join I2C bus (I2Cdev library doesn't do this automatically)
    #if I2CDEV_IMPLEMENTATION == I2CDEV_ARDUINO_WIRE
        Wire.begin();
        Wire.setClock(400000); // 400kHz I2C clock. Comment this line if having compilation difficulties
    #elif I2CDEV_IMPLEMENTATION == I2CDEV_BUILTIN_FASTWIRE
        Fastwire::setup(400, true);
    #endif

    // initialize serial communication
    // (115200 chosen because it is required for Teapot Demo output, but it's
    // really up to you depending on your project)
    Serial.begin(115200);
    while (!Serial); // wait for Leonardo enumeration, others continue immediately

    // NOTE: 8MHz or slower host processors, like the Teensy @ 3.3V or Arduino
    // Pro Mini running at 3.3V, cannot handle this baud rate reliably due to
    // the baud timing being too misaligned with processor ticks. You must use
    // 38400 or slower in these cases, or use some kind of external separate
    // crystal solution for the UART timer.

    // initialize device
    Serial.println(F("Initializing I2C devices..."));
    mpu.initialize();
    pinMode(INTERRUPT_PIN, INPUT);

    // verify connection
    Serial.println(F("Testing device connections..."));
    Serial.println(mpu.testConnection() ? F("MPU6050 connection successful") : F("MPU6050 connection failed"));

    // wait for ready
    Serial.println(F("\nSend any character to begin DMP programming and demo: "));
    while (Serial.available() && Serial.read()); // empty buffer
    while (!Serial.available());                 // wait for data
    while (Serial.available() && Serial.read()); // empty buffer again

    // load and configure the DMP
    Serial.println(F("Initializing DMP..."));
    devStatus = mpu.dmpInitialize();

    // supply your own gyro offsets here, scaled for min sensitivity
    mpu.setXGyroOffset(220);
    mpu.setYGyroOffset(76);
    mpu.setZGyroOffset(-85);
    mpu.setZAccelOffset(1788); // 1688 factory default for my test chip

    // make sure it worked (returns 0 if so)
    if (devStatus == 0) {
        // turn on the DMP, now that it's ready
        Serial.println(F("Enabling DMP..."));
        mpu.setDMPEnabled(true);

        // enable Arduino interrupt detection
        Serial.println(F("Enabling interrupt detection (Arduino external interrupt 0)..."));
        attachInterrupt(digitalPinToInterrupt(INTERRUPT_PIN), dmpDataReady, RISING);
        mpuIntStatus = mpu.getIntStatus();

        // set our DMP Ready flag so the main loop() function knows it's okay to use it
        Serial.println(F("DMP ready! Waiting for first interrupt..."));
        dmpReady = true;

        // get expected DMP packet size for later comparison
        packetSize = mpu.dmpGetFIFOPacketSize();
    } else {
        // ERROR!
        // 1 = initial memory load failed
        // 2 = DMP configuration updates failed
        // (if it's going to break, usually the code will be 1)
        Serial.print(F("DMP Initialization failed (code "));
        Serial.print(devStatus);
        Serial.println(F(")"));
    }

    // configure LED for output
    pinMode(LED_PIN, OUTPUT);
}



// ================================================================
// ===                    MAIN PROGRAM LOOP                     ===
// ================================================================

void readIMU() {
    // if programming failed, don't try to do anything
    if (!dmpReady) return;

    // wait for MPU interrupt or extra packet(s) available
    while (!mpuInterrupt && fifoCount < packetSize) {
        // other program behavior stuff here
        // .
        // .
        // .
        // if you are really paranoid you can frequently test in between other
        // stuff to see if mpuInterrupt is true, and if so, "break;" from the
        // while() loop to immediately process the MPU data
        // .
        // .
        // .
    }

    // reset interrupt flag and get INT_STATUS byte
    mpuInterrupt = false;
    mpuIntStatus = mpu.getIntStatus();

    // get current FIFO count
    fifoCount = mpu.getFIFOCount();

    // check for overflow (this should never happen unless our code is too inefficient)
    if ((mpuIntStatus & 0x10) || fifoCount == 1024) {
        // reset so we can continue cleanly
        mpu.resetFIFO();
        Serial.println(F("FIFO overflow!"));

    // otherwise, check for DMP data ready interrupt (this should happen frequently)
    } else if (mpuIntStatus & 0x02) {
        // wait for correct available data length, should be a VERY short wait
        while (fifoCount < packetSize) fifoCount = mpu.getFIFOCount();

        // read a packet from FIFO
        mpu.getFIFOBytes(fifoBuffer, packetSize);

        // track FIFO count here in case there is > 1 packet available
        // (this lets us immediately read more without waiting for an interrupt)
        fifoCount -= packetSize;

        #ifdef OUTPUT_READABLE_QUATERNION
            // display quaternion values in easy matrix form: w x y z
            mpu.dmpGetQuaternion(&q, fifoBuffer);
            Serial.print("quat\t");
            Serial.print(q.w);
            Serial.print("\t");
            Serial.print(q.x);
            Serial.print("\t");
            Serial.print(q.y);
            Serial.print("\t");
            Serial.println(q.z);
        #endif

        #ifdef OUTPUT_READABLE_EULER
            // display Euler angles in degrees
            mpu.dmpGetQuaternion(&q, fifoBuffer);
            mpu.dmpGetEuler(euler, &q);

            Serial.print("euler\t");
            Serial.print(euler[0] * 180/M_PI);
            Serial.print("\t");
            Serial.print(euler[1] * 180/M_PI);
            Serial.print("\t");
            Serial.println(euler[2] * 180/M_PI);
        #endif

        #ifdef OUTPUT_READABLE_YAWPITCHROLL
            // display Euler angles in degrees
            mpu.dmpGetQuaternion(&q, fifoBuffer);
            mpu.dmpGetGravity(&gravity, &q);
            mpu.dmpGetYawPitchRoll(ypr, &q, &gravity);

            yaw = ypr[0] * 180/M_PI;
            pitch = ypr[1] * 180/M_PI;
            roll = ypr[2] * 180/M_PI;
//
//            Serial.print("ypr\t");
//            Serial.print(yaw);
//            Serial.print("\t");
//            Serial.print(pitch);
//            Serial.print("\t");
//            Serial.println(roll);
        #endif

        #ifdef OUTPUT_READABLE_REALACCEL
            // display real acceleration, adjusted to remove gravity
            mpu.dmpGetQuaternion(&q, fifoBuffer);
            mpu.dmpGetAccel(&aa, fifoBuffer);
            mpu.dmpGetGravity(&gravity, &q);
            mpu.dmpGetLinearAccel(&aaReal, &aa, &gravity);
            Serial.print("areal\t");
            Serial.print(aaReal.x);
            Serial.print("\t");
            Serial.print(aaReal.y);
            Serial.print("\t");
            Serial.println(aaReal.z);
        #endif

        #ifdef OUTPUT_READABLE_WORLDACCEL
            // display initial world-frame acceleration, adjusted to remove gravity
            // and rotated based on known orientation from quaternion
            mpu.dmpGetQuaternion(&q, fifoBuffer);
            mpu.dmpGetAccel(&aa, fifoBuffer);
            mpu.dmpGetGravity(&gravity, &q);
            mpu.dmpGetLinearAccel(&aaReal, &aa, &gravity);
            mpu.dmpGetLinearAccelInWorld(&aaWorld, &aaReal, &q);
            Serial.print("aworld\t");
            Serial.print(aaWorld.x);
            Serial.print("\t");
            Serial.print(aaWorld.y);
            Serial.print("\t");
            Serial.println(aaWorld.z);
        #endif

        #ifdef OUTPUT_TEAPOT
            // display quaternion values in InvenSense Teapot demo format:
            teapotPacket[2] = fifoBuffer[0];
            teapotPacket[3] = fifoBuffer[1];
            teapotPacket[4] = fifoBuffer[4];
            teapotPacket[5] = fifoBuffer[5];
            teapotPacket[6] = fifoBuffer[8];
            teapotPacket[7] = fifoBuffer[9];
            teapotPacket[8] = fifoBuffer[12];
            teapotPacket[9] = fifoBuffer[13];
            Serial.write(teapotPacket, 14);
            teapotPacket[11]++; // packetCount, loops at 0xFF on purpose
        #endif

        // blink LED to indicate activity
        blinkState = !blinkState;
        digitalWrite(LED_PIN, blinkState);
    }
}

void setupStepper(){  // Set a PWM signal to the step pins with 50% duty cycle
  pinMode(DIR1, OUTPUT);          // sets the digital pin 13 as output
  pinMode(DIR2, OUTPUT);          // sets the digital pin 13 as output
  pinMode(DIR3, OUTPUT);          // sets the digital pin 13 as output

  analogWrite(STEP1, 10);
  analogWrite(STEP2, 10);
  analogWrite(STEP3, 10);
}

void updateMotors(long stepHz1, long stepHz2, long stepHz3){
  if (stepHz1 < 0){
    digitalWrite(DIR1,LOW);
  }
  else{
    digitalWrite(DIR1,HIGH);
  }
  analogWriteFrequency(STEP1, abs(stepHz1)); // pins 3 also change
 

  if (stepHz2 < 0){
    digitalWrite(DIR2,LOW);
  }
  else{
    digitalWrite(DIR2,HIGH);
  }
  analogWriteFrequency(STEP2, abs(stepHz2)); // pins 3 also change


  if (stepHz3 < 0){
    digitalWrite(DIR3,LOW);
  }
  else{
    digitalWrite(DIR3,HIGH);
  }
  analogWriteFrequency(STEP3, abs(stepHz3)); // pins 3 also change
}

void speedCalculations(){
  // Convert PID output to inches per second
  int speedX = map(OutputSpeedX,0,255,0,MAX_SPEED);
  int speedY = map(OutputSpeedY,0,255,0,MAX_SPEED);
  int speedZ = map(OutputSpeedZ,0,255,0,MAX_SPEED);
//  Serial.print("Speed-x: "); Serial.println(speedX);
//  Serial.print("Speed-y: "); Serial.println(speedY);
//  Serial.print("Speed-z: "); Serial.println(speedZ);
  if (pitch < 0){
    speedX = -speedX;
  }
  if (roll < 0){
    speedY = -speedY;
  }
  // if (yaw < 0){
  //   speedZ = -speedZ;
  // }

  // from inches per second to steps per sec
  speed1 = ((-(speedX/2)+(0.866*speedY)+speedZ)/(2*PI*WHEEL_RADIUS))*STEPS_PER_ROTATION;
  speed2 = ((-(speedX/2)-(0.866*speedY)+speedZ)/(2*PI*WHEEL_RADIUS))*STEPS_PER_ROTATION;
  speed3 = ((speedX+speedZ)/(2*PI*WHEEL_RADIUS))*STEPS_PER_ROTATION;
}

void setupPID(){
  xPID.SetMode(AUTOMATIC);
  yPID.SetMode(AUTOMATIC);
  zPID.SetMode(AUTOMATIC);
}

void setup(){
  setupIMU();
  setupPID();
  setupStepper();
}

void loop(){

  readIMU();
  CurrentAngleX = (double)-abs(pitch);
  CurrentAngleY = (double)-abs(roll);
  //  CurrentAngleZ = (double)-abs(yaw);
  
  timer = micros() - timerstart;
  if (timer>=sampleRate){
    xPID.Compute();
    yPID.Compute();
    zPID.Compute();
    speedCalculations();
    updateMotors(speed1, speed2, speed3);
    timerstart = micros();
  
    Serial.print("X-angle: "); Serial.print(CurrentAngleX);
    Serial.print(" X-speed: "); Serial.println(OutputSpeedX);
    Serial.print("Y-angle: "); Serial.print(CurrentAngleY);
    Serial.print(" Y-speed: "); Serial.println(OutputSpeedY);
    Serial.print("Z-angle: "); Serial.print(CurrentAngleZ);
    Serial.print(" Z-speed: "); Serial.println(OutputSpeedZ);

    Serial.print("Motor 1 Speed: "); Serial.println(speed1);
    Serial.print("Motor 2 Speed: "); Serial.println(speed2);
    Serial.print("Motor 3 Speed: "); Serial.println(speed3);
    Serial.print("Timer: "); Serial.println(timer);
  }
}

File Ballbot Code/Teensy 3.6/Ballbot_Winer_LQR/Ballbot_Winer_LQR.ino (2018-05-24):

/* Ballbot_MPU6050.ino
*
* Omnidirectional Ballbot control system with 3-axis PID controls using the
* MPU6050 IMU
*
* Written by Adam Woo
*
* MIT License
*/

#include "quaternionFilters.h"
#include "math.h"
#include "discreteSSC.h"
#include "Wire.h"
#include "FrequencyTimer2.h"
#include "TimerOne.h"
#include "TimerThree.h"

#define MAXSPEED 20000 //steps per second
#define WHEEL_RADIUS 0.041275 //meters
#define STEPS_PER_ROTATION 1600 //steps
#define METERS_PER_ROTATION 0.25933908 //meters
#define X 0
#define X_dot 1
#define Theta 2
#define Theta_dot 3

// Gains calculated in Matlab
double K[4] = {-3.1534,  -11.1431,  418.2550,   36.6484}; // Ts = .01
//double K[4] = {-3.8233,  -11.6122,  157.3357,   15.1280}; // Ts = .05
//double K[4] = {-6.6584,  -71.0167,  429.0208,   53.3783}; // Ts = .005

long double Ts = 0.01;  // seconds

//double A[4][4] = {
//   {0,         1,         0,         0},
//   {0,   -0.1176,   88.8671,         0},
//   {0,         0,         0,         1},
//   {0,   -0.2941,  246.6926,         0}
//};

// m=7.7 b=1
//double A[4][4] = {
//   {0,         1,         0,         0},
//   {0,   -1.1765,   88.8671,         0},
//   {0,         0,         0,         1},
//   {0,   -2.9412,  246.6926,         0}
//};

// m=8
double A[4][4] = {
   {0,         1,         0,         0},
   {0,   -0.0799,   53.3002,         0},
   {0,         0,         0,         1},
   {0,   -0.3773,  595.9257,         0}
};

double B[4][1]={
  {      0},
  { 0.7992},
  {      0},
  { 3.7731}
};

//double B[4][1]={
//  {      0},
//  { 1.1765},
//  {      0},
//  { 3.9216}
//};

double C[1][4]={
  {0, 0, 1, 0}
};

double D[1][1]={
  {0}
};

long double Setpoints[4][1]={
  {0},
  {0},
  {0},
  {0}
};

long double Inputs[4][1]={
  {0},
  {0},
  {0},
  {0}
};

long double Outputs[4][1]={
  {0},
  {0},
  {0},
  {0}
};

long double xAngle, yAngle, zAngle, AVx, AVy;
long double OutputX, OutputY, OutputZ, currentOutputX, currentOutputY;
long currentSpeed1, currentSpeed2, currentSpeed3;

SSC xSSC(A, B, K, Ts, Setpoints, Inputs, Outputs);
SSC ySSC(A, B, K, Ts, Setpoints, Inputs, Outputs);
// SSC zSSC(A, B, K, Ts, Setpoints, Inputs, Outputs);

bool printFlag = false;

#define DIR1 12
#define STEP1 2
#define DIR2 24
#define STEP2 3
#define DIR3 26
#define STEP3 5


#define AHRS true         // Set to false for basic data read
#define SerialDebug true  // Set to true to get Serial output for debugging

// -----------------------------------------------------------------------------
// Need this to compile for some reason... No idea why. Think it has something
// to do with the way the Teensy loader works
extern "C"{
  int _getpid(){ return -1;}
  int _kill(int pid, int sig){ return -1; }
  int _write(){return -1;}
}
// -----------------------------------------------------------------------------

// Pin definitions
int Pin = 12;  // These can be changed, 2 and 3 are the Arduinos ext int pins
int RPM = 0;

int startMotors=0;
long double speed1, speed2, speed3;
long double timer = 0, timerstart, timerend;

// -----------------------------------------------------------------------------
#define XGOFFS_TC        0x00 // Bit 7 PWR_MODE, bits 6:1 XG_OFFS_TC, bit 0 OTP_BNK_VLD
#define YGOFFS_TC        0x01
#define ZGOFFS_TC        0x02
#define X_FINE_GAIN      0x03 // [7:0] fine gain
#define Y_FINE_GAIN      0x04
#define Z_FINE_GAIN      0x05
#define XA_OFFSET_H      0x06 // User-defined trim values for accelerometer
#define XA_OFFSET_L_TC   0x07
#define YA_OFFSET_H      0x08
#define YA_OFFSET_L_TC   0x09
#define ZA_OFFSET_H      0x0A
#define ZA_OFFSET_L_TC   0x0B
#define SELF_TEST_X      0x0D
#define SELF_TEST_Y      0x0E
#define SELF_TEST_Z      0x0F
#define SELF_TEST_A      0x10
#define XG_OFFS_USRH     0x13  // User-defined trim values for gyroscope; supported in MPU-6050?
#define XG_OFFS_USRL     0x14
#define YG_OFFS_USRH     0x15
#define YG_OFFS_USRL     0x16
#define ZG_OFFS_USRH     0x17
#define ZG_OFFS_USRL     0x18
#define SMPLRT_DIV       0x19
#define CONFIG           0x1A
#define GYRO_CONFIG      0x1B
#define ACCEL_CONFIG     0x1C
#define FF_THR           0x1D  // Free-fall
#define FF_DUR           0x1E  // Free-fall
#define MOT_THR          0x1F  // Motion detection threshold bits [7:0]
#define MOT_DUR          0x20  // Duration counter threshold for motion interrupt generation, 1 kHz rate, LSB = 1 ms
#define ZMOT_THR         0x21  // Zero-motion detection threshold bits [7:0]
#define ZRMOT_DUR        0x22  // Duration counter threshold for zero motion interrupt generation, 16 Hz rate, LSB = 64 ms
#define FIFO_EN          0x23
#define I2C_MST_CTRL     0x24
#define I2C_SLV0_ADDR    0x25
#define I2C_SLV0_REG     0x26
#define I2C_SLV0_CTRL    0x27
#define I2C_SLV1_ADDR    0x28
#define I2C_SLV1_REG     0x29
#define I2C_SLV1_CTRL    0x2A
#define I2C_SLV2_ADDR    0x2B
#define I2C_SLV2_REG     0x2C
#define I2C_SLV2_CTRL    0x2D
#define I2C_SLV3_ADDR    0x2E
#define I2C_SLV3_REG     0x2F
#define I2C_SLV3_CTRL    0x30
#define I2C_SLV4_ADDR    0x31
#define I2C_SLV4_REG     0x32
#define I2C_SLV4_DO      0x33
#define I2C_SLV4_CTRL    0x34
#define I2C_SLV4_DI      0x35
#define I2C_MST_STATUS   0x36
#define INT_PIN_CFG      0x37
#define INT_ENABLE       0x38
#define DMP_INT_STATUS   0x39  // Check DMP interrupt
#define INT_STATUS       0x3A
#define ACCEL_XOUT_H     0x3B
#define ACCEL_XOUT_L     0x3C
#define ACCEL_YOUT_H     0x3D
#define ACCEL_YOUT_L     0x3E
#define ACCEL_ZOUT_H     0x3F
#define ACCEL_ZOUT_L     0x40
#define TEMP_OUT_H       0x41
#define TEMP_OUT_L       0x42
#define GYRO_XOUT_H      0x43
#define GYRO_XOUT_L      0x44
#define GYRO_YOUT_H      0x45
#define GYRO_YOUT_L      0x46
#define GYRO_ZOUT_H      0x47
#define GYRO_ZOUT_L      0x48
#define EXT_SENS_DATA_00 0x49
#define EXT_SENS_DATA_01 0x4A
#define EXT_SENS_DATA_02 0x4B
#define EXT_SENS_DATA_03 0x4C
#define EXT_SENS_DATA_04 0x4D
#define EXT_SENS_DATA_05 0x4E
#define EXT_SENS_DATA_06 0x4F
#define EXT_SENS_DATA_07 0x50
#define EXT_SENS_DATA_08 0x51
#define EXT_SENS_DATA_09 0x52
#define EXT_SENS_DATA_10 0x53
#define EXT_SENS_DATA_11 0x54
#define EXT_SENS_DATA_12 0x55
#define EXT_SENS_DATA_13 0x56
#define EXT_SENS_DATA_14 0x57
#define EXT_SENS_DATA_15 0x58
#define EXT_SENS_DATA_16 0x59
#define EXT_SENS_DATA_17 0x5A
#define EXT_SENS_DATA_18 0x5B
#define EXT_SENS_DATA_19 0x5C
#define EXT_SENS_DATA_20 0x5D
#define EXT_SENS_DATA_21 0x5E
#define EXT_SENS_DATA_22 0x5F
#define EXT_SENS_DATA_23 0x60
#define MOT_DETECT_STATUS 0x61
#define I2C_SLV0_DO      0x63
#define I2C_SLV1_DO      0x64
#define I2C_SLV2_DO      0x65
#define I2C_SLV3_DO      0x66
#define I2C_MST_DELAY_CTRL 0x67
#define SIGNAL_PATH_RESET  0x68
#define MOT_DETECT_CTRL   0x69
#define USER_CTRL        0x6A  // Bit 7 enable DMP, bit 3 reset DMP
#define PWR_MGMT_1       0x6B // Device defaults to the SLEEP mode
#define PWR_MGMT_2       0x6C
#define DMP_BANK         0x6D  // Activates a specific bank in the DMP
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

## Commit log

2017-01-01 PID fix
2017-11-23 Setup Teensy code
2018-02-28 Set Sample Rate
2018-02-28 IMU Fix
2018-03-04 Stepper Testing
2018-03-25 Motor Testing
    [Ballbot Motor Mount v.3.stl, Wheel Mount.stl]
2018-03-27 Update PWM
2018-04-04 Sample Rate
2018-04-24 Kinematics Update
